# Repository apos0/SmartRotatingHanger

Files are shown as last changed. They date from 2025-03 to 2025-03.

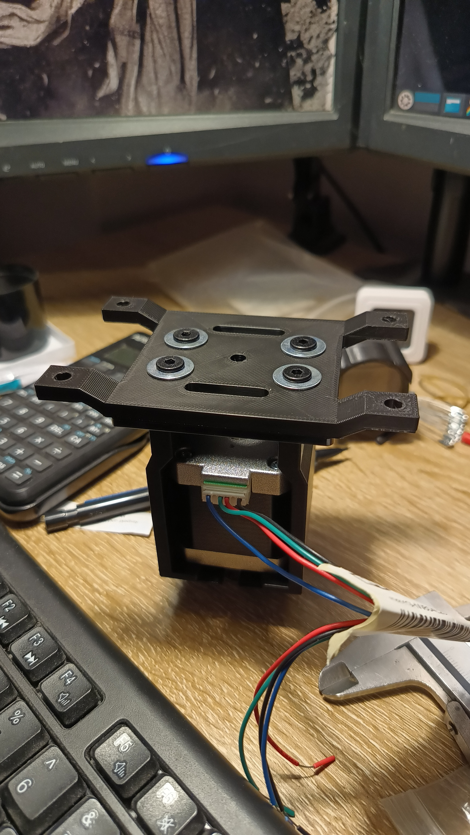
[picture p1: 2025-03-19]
media/IMG-48fe138d9beb614020ce367cf5287fd0-V.jpg

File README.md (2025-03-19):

# Smart Rotating Hanger  

**NOTE:** This project was designed within a few days and is not fully operational. There will be no updates on this repository. However, you are free to study, improve, and fork it.  

This project is licensed under **GPL3**, allowing you to use it within the extent permitted by the license.  

## Overview  
Smart Rotating Hanger is an Arduino-based system that automates the rotation of a circular dress hanger. Users can adjust the rotation speed using an encoder, and an OLED screen displays the current RPM.  

## Features  
- Adjustable rotation speed using a rotary encoder  
- Real-time RPM display on an OLED screen  
- Controlled by an **Arduino Nano**  
- Stepper motor-driven rotation for smooth operation  

## Basic Components  
- **Arduino Nano**  
- **Stepper Motor** (42BYGHW804)  
- **Stepper Motor Controller** (DRV8825)  
- **Rotary Encoder**  
- **OLED Display** (GME12864)  
- **12V 6A Power Supply**  

## Extended Components  

### Mechanical Parts  
- [Gantry Plate](https://grobotronics.com/v-slot-gantry-plate-20mmoem.html) x1  
- [Shaft Hub 5mm](https://grobotronics.com/shaft-hub-5mm.html) x1  
- [Bolt M3 L50](https://grobotronics.com/m3-l50mm-cheese-head-philips.html) x4  
- [Bolt M3 L10](https://grobotronics.com/bolt-m3-din-912.html?variation_id=11809) x4  
- [Bolt M3 L5](https://grobotronics.com/bolt-m3-din7985-black-100pcs.html) x4  
- [Nut M3](https://grobotronics.com/nut-safety-m3-metal.html) x4  
- [Bolt M5 L15](https://grobotronics.com/bolt-m5-low-profile-black.html?variation_id=15208) x4  
- [Washer M5](https://grobotronics.com/washer-m5mm.html) x4  

### Electronics  
- [Stepper Motor](https://grobotronics.com/stepper-motor-42byghw804.html)  
- [DRV8825 Driver](https://grobotronics.com/drv8825-stepper-motor-driver.html)  
- [Arduino Nano](https://grobotronics.com/nano-compatible-ch340-with-headers.html)  
- [PCB Board](https://grobotronics.com/72x47mm.html)  
- [OLED Display](https://grobotronics.com/oled-module-1.3-128x64-i2c-white.html)  
- [Rotary Encoder](https://grobotronics.com/rotary-encoder-module-for-arduino-rectangle-pcb.html)  
- [Encoder Knob](https://grobotronics.com/potentiometer-knob-17x14mm-grey-d-shaft.html)  
- [Power Supply](https://grobotronics.com/rotary-encoder-module-for-arduino-rectangle-pcb.html)  
- [Rocker Switch](https://grobotronics.com/rocker-switch-on-off-blackdaier.html)  

## Problems & Notes  
- Unfortunately, the project did not work as intended. The stepper motor was not strong enough to handle the dress's weight.  
- The **DRV8825 driver** overheated after a few minutes. This was patched by adding an **80mm 12V fan** on top of the enclosure box.  
- The stepper motor overheated, likely due to the dress’s inertia on each rotation change.  
- The motor overheating caused the **M5 bolts** on the motor mount to loosen, leading to the mount falling.  

### Conclusion  
A **larger stepper motor** or switching to a **more powerful DC motor** would be required for better performance.

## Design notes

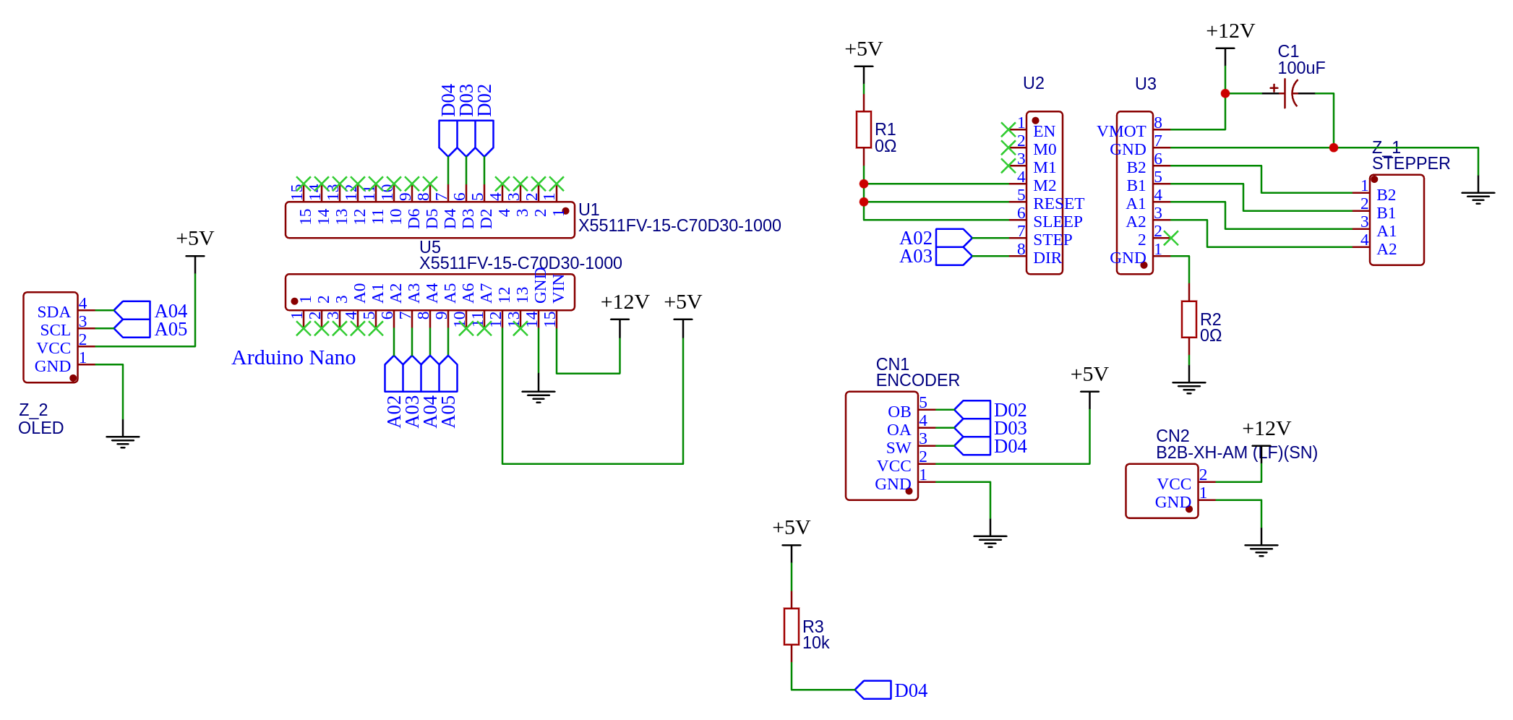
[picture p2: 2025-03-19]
media/schematic_view.png

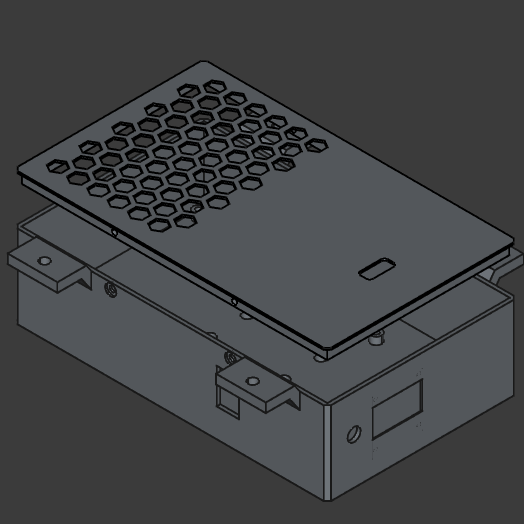
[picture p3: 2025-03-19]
media/Screenshot_20250210_215321.png

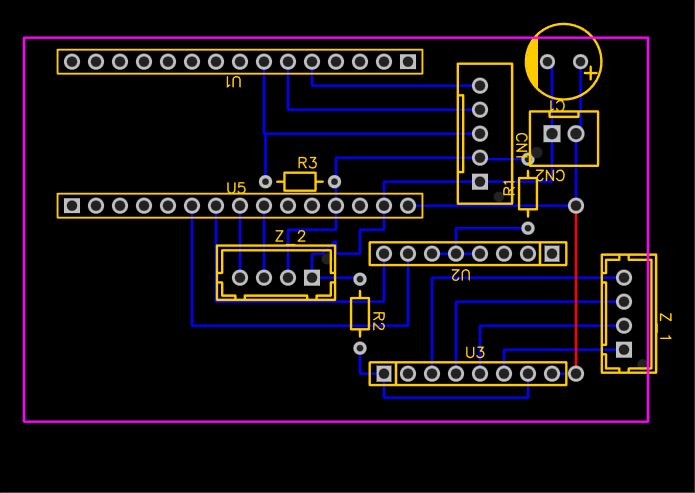
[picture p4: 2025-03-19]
media/pcb_view.png

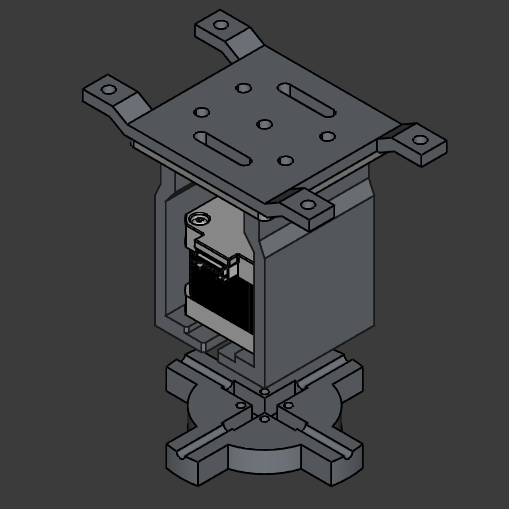
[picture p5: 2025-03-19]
media/Screenshot_20250210_141416.png

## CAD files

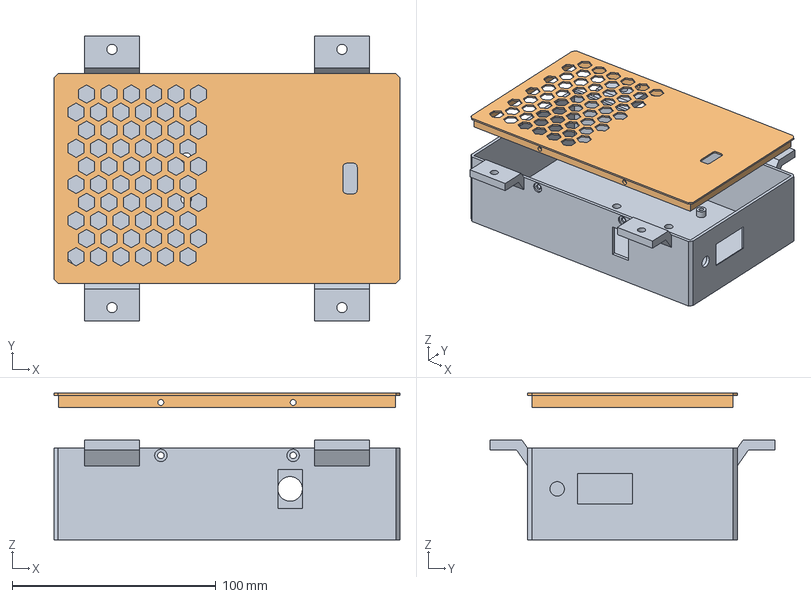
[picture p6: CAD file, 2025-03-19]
freecad/electronicsShell.FCStd
170.0 x 139.8 x 72.0 mm

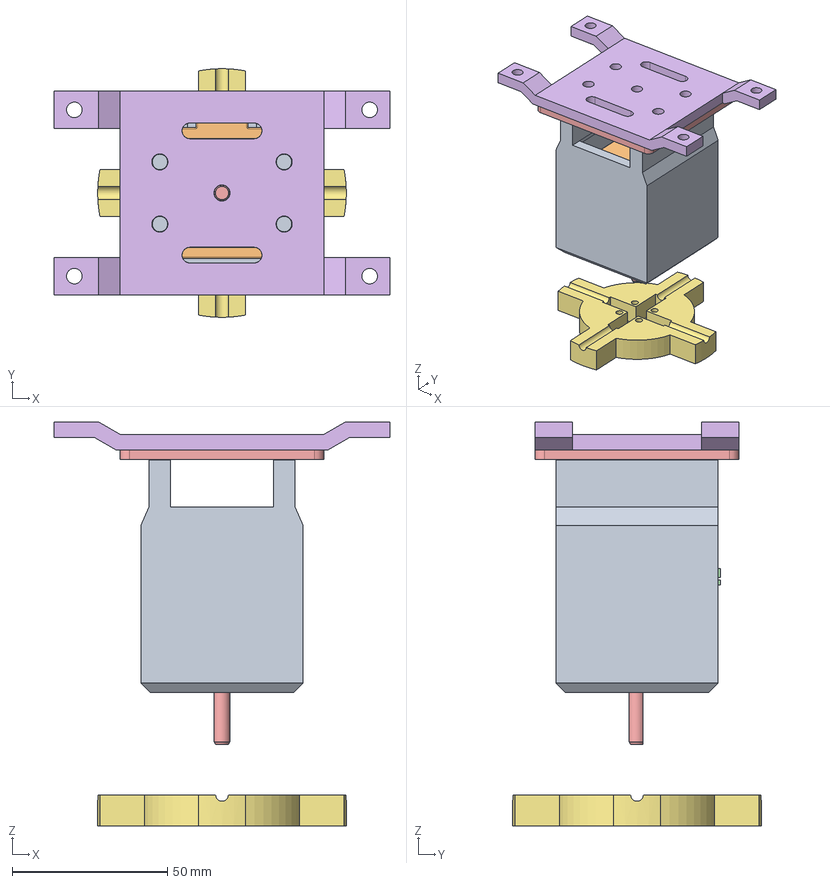
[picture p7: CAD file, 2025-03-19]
freecad/MotorMount.FCStd
108.0 x 80.0 x 130.0 mm
stepperMount
rear end cap
rear bearing
connector
shaft
stator
front end cap
front bearing
M3x10-Screw
M3x10-Screw001
M3x10-Screw002
M3x10-Screw003
V-Slot Gantry Plate 20mm v1
ceilingMount
hangerHolder

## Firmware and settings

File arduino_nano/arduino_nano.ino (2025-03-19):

#include <AccelStepper.h>
#include <MultiStepper.h>
#include <Adafruit_SSD1306.h>
#include <splash.h>
#include <RotaryEncoder.h>

//Define encoder pins
#define ENCODER_A 3
#define ENCODER_B 2
#define ENCODER_SW 4
#define ENCODER_DIRECTION 1  //Change to -1 to switch direction of encoder
//Define stepper driver pins
#define DRIVER_STEP 16
#define DRIVER_DIR 17
#define motorInterfaceType 1
#define STEPPER_SPR 3200  //Define stepper motor steps per revolution

RotaryEncoder encoder(ENCODER_A, ENCODER_B, RotaryEncoder::LatchMode::TWO03);
Adafruit_SSD1306 display(128, 64, &Wire, -1);

void oledPrint(int printInt);
int rotarySelect(int currentVal, int maxVal, int minVal);
AccelStepper stepper = AccelStepper(motorInterfaceType, DRIVER_STEP, DRIVER_DIR);


const short maxRpm = 500;
const short minRpm = 1;
//short previousRpm = 0;
short selectedRpm = 60;
short currentRpm = 60;
short printVal = 60;
short savedRpm = 0;
unsigned long time01 = 0;
short stepperDirection = 1;

void setup() {
  Serial.begin(9600);

  if (!display.begin(SSD1306_SWITCHCAPVCC, 0x3C)) {
    Serial.println(F("SSD1306 allocation failed"));
    for (;;)
      ;  // Don't proceed, loop forever
  }
  display.clearDisplay();
  display.setTextColor(SSD1306_WHITE);
  display.setTextSize(2);
  //display.println("SmartRotatingHanger");
  display.print("github.com/apos0");
  display.display();
  delay(3000);
  display.setTextSize(3);
  pinMode(ENCODER_SW, INPUT);
  stepper.setMaxSpeed(maxRpm * (STEPPER_SPR / 60));
  stepper.setSpeed(currentRpm * (STEPPER_SPR / 60));
  time01 = millis();
}

void loop() {

  //Change direction every 15seconds




  if (printVal == 1000 || printVal == 1001) {
    if (printVal == 1001) {
      if (selectedRpm == 0) {
        selectedRpm = savedRpm;
      } else {
        savedRpm = selectedRpm;
        selectedRpm = 0;
      }
      //delay(1000);
    }
    currentRpm = selectedRpm;
    stepper.setSpeed(stepperDirection * currentRpm * (STEPPER_SPR / 60));
  } else if (selectedRpm != 0)
    selectedRpm = printVal;

  oledPrint(selectedRpm);

  printVal = rotarySelect(selectedRpm, maxRpm, minRpm);
}


int rotarySelect(int currentVal, int maxVal, int minVal) {
  static int encPos = 0;
  while (1) {
    stepper.runSpeed();
    if (millis() - time01 >= 60000) {
      time01 = millis();
      stepperDirection *= -1;
      stepper.setSpeed(stepperDirection * currentRpm * (STEPPER_SPR / 60));
    }
    encoder.tick();
    int newPos = encoder.getPosition();

    if (newPos != encPos) {
      int direction = ((int)(encoder.getDirection()));
      switch (direction) {
        case (-1 * ENCODER_DIRECTION):
          if (currentVal > minVal) currentVal--;
          break;

        case (1 * ENCODER_DIRECTION):
          if (currentVal < maxVal) currentVal++;
          break;
      }
      encPos = newPos;
      //delay(20);
      return currentVal;
    }

    if (digitalRead(ENCODER_SW) == 0) {
      unsigned long temp1 = millis();
      while (digitalRead(ENCODER_SW) == 0)
        if ((millis() - temp1) >= 2000) return 1001;

      delay(100);
      return 1000;
    }
  }
}

void oledPrint(int printInt) {
  display.clearDisplay();
  if (printInt == 0) {
    display.setCursor(25, 20);
    display.print(F("STOP"));
  } else {
    display.setCursor(0, 20);
    display.print(F("RPM:"));
    display.println(printInt);
  }
  display.display();
}
